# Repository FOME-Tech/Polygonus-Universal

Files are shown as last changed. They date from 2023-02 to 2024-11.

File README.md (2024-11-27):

# Polygonus-Universal

Basic pinout for the bosch 88 pin plug intended for universal use.  

## NOT COMPATIBLE WITH ANY PNP APPLICATION  

## NOTE - 88pin plug is now hard to source as it seems to be NLA from Aliexpress. 
Hardware tested ok on the first fabrication but is now obsolete due to connector sourcing issues. 
Board is provided as is for reference of if someone wants to fabricate and source their own connectors.

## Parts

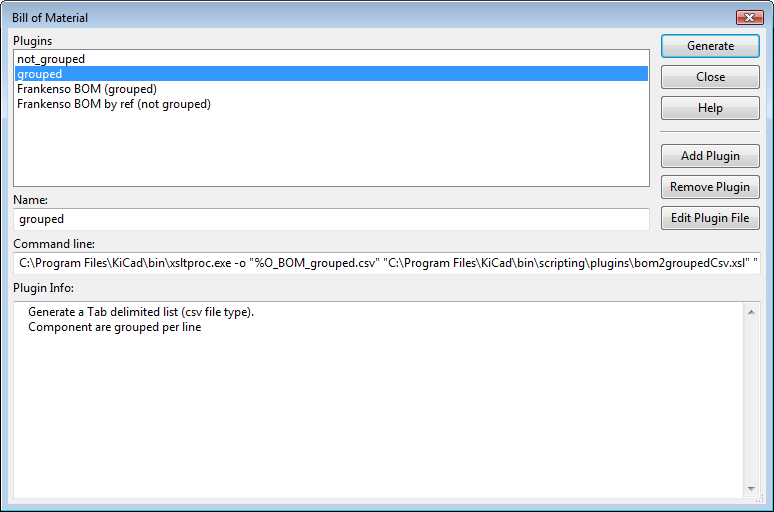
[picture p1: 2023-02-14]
kicad-libraries/BOM_related/Kicad_BOM_grouped.png

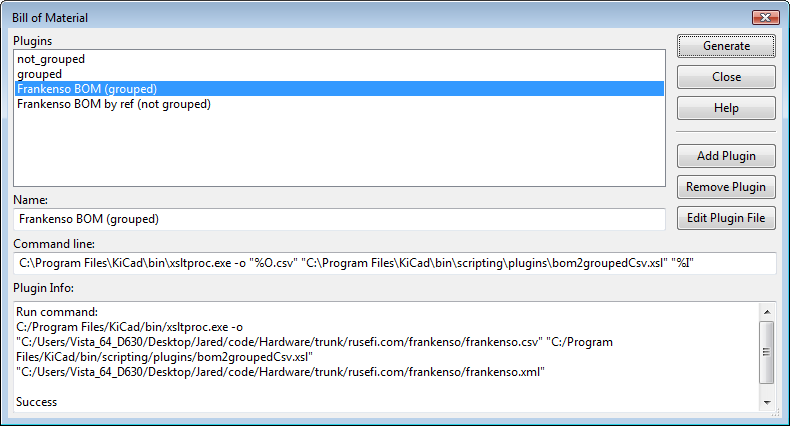
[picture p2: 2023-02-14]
kicad-libraries/BOM_related/Kicad_BOM_grouped_Frankenso.png

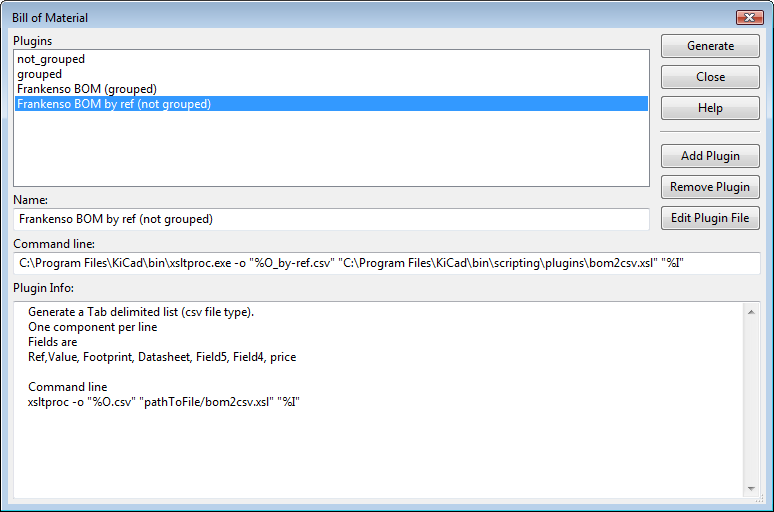
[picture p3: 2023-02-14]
kicad-libraries/BOM_related/Kicad_BOM_Not_grouped_Frankenso.png

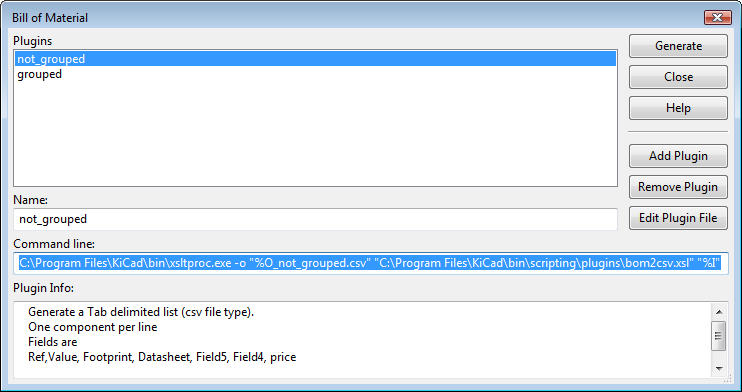
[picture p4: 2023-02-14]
kicad-libraries/BOM_related/Kicad_BOM_Not_grouped.png

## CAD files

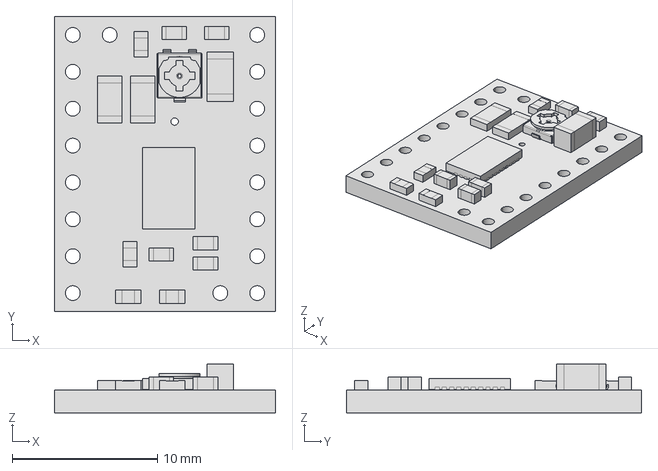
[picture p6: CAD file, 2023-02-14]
kicad-libraries/3d/Misc/drv8880-stepper-motor-driver-carrier.FCStd
15.2 x 20.3 x 3.37 mm

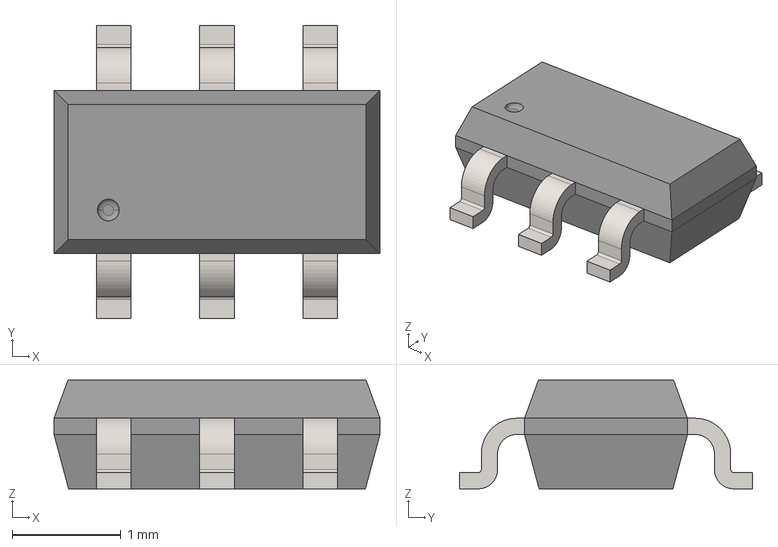
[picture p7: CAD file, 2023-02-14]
kicad-libraries/3d/TSOP-6.step
3.00 x 2.70 x 1.00 mm

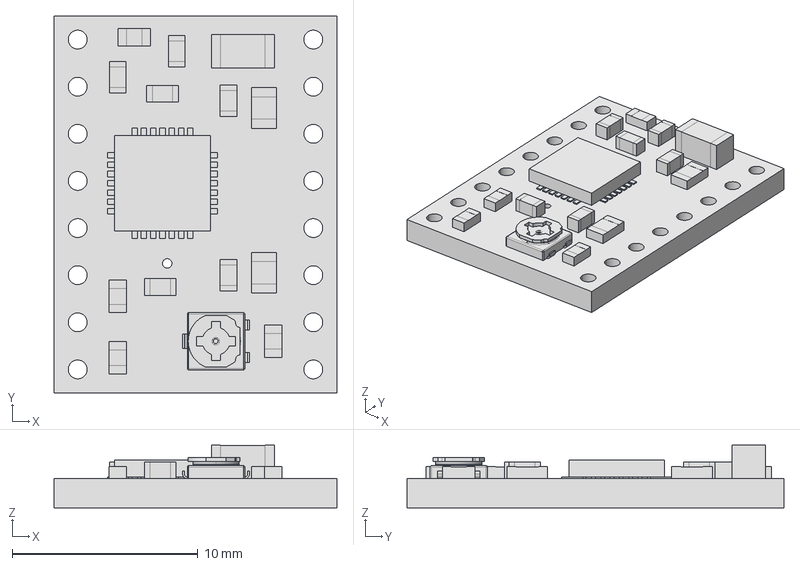
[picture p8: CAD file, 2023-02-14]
kicad-libraries/3d/Misc/a4988-stepper-motor-driver-carrier.FCStd
15.2 x 20.3 x 3.37 mm

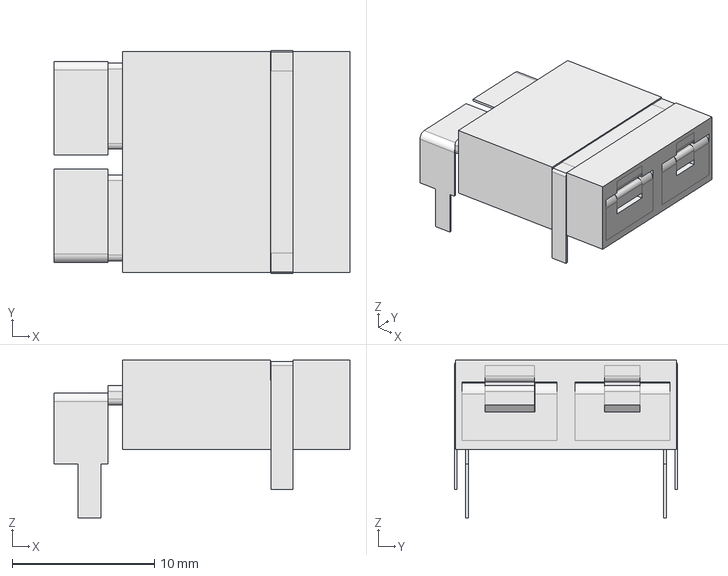
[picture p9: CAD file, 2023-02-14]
kicad-libraries/3d/TCPL_CONNECTOR_PCC-SMP.step
20.8 x 15.7 x 11.1 mm

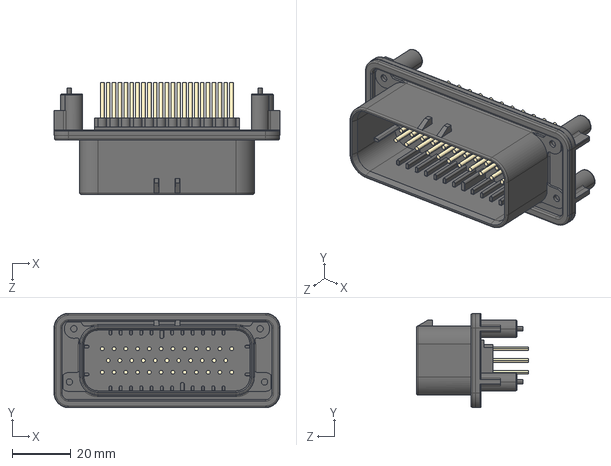
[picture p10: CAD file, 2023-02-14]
kicad-libraries/3d/c-1-776231-1-d-3d.STEP
76.9 x 32.1 x 38.0 mm

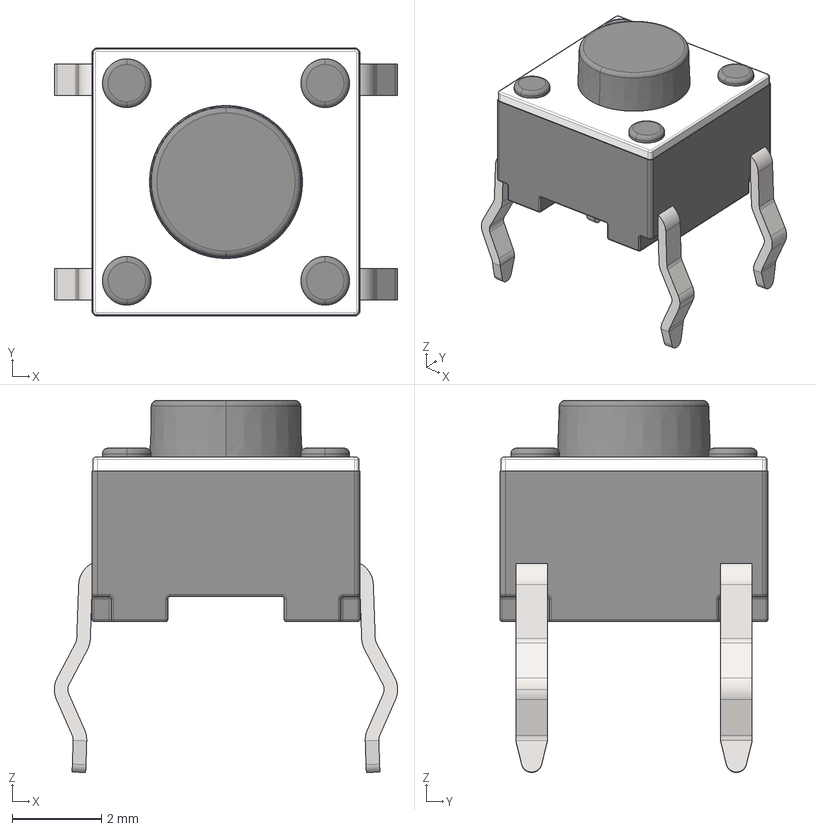
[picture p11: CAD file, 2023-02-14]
kicad-libraries/3d/tactileswitch-short.step
7.69 x 6.01 x 8.33 mm

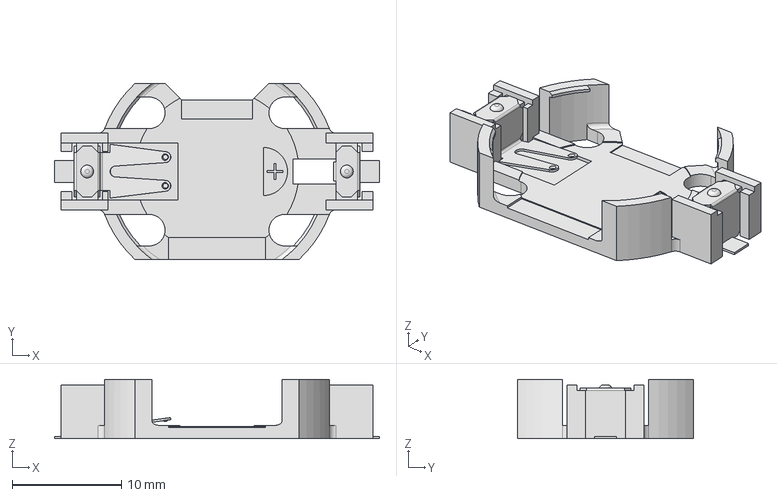
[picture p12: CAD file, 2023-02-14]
kicad-libraries/3d/BatHolder_SMTU2032.step
29.7 x 16.1 x 5.40 mm

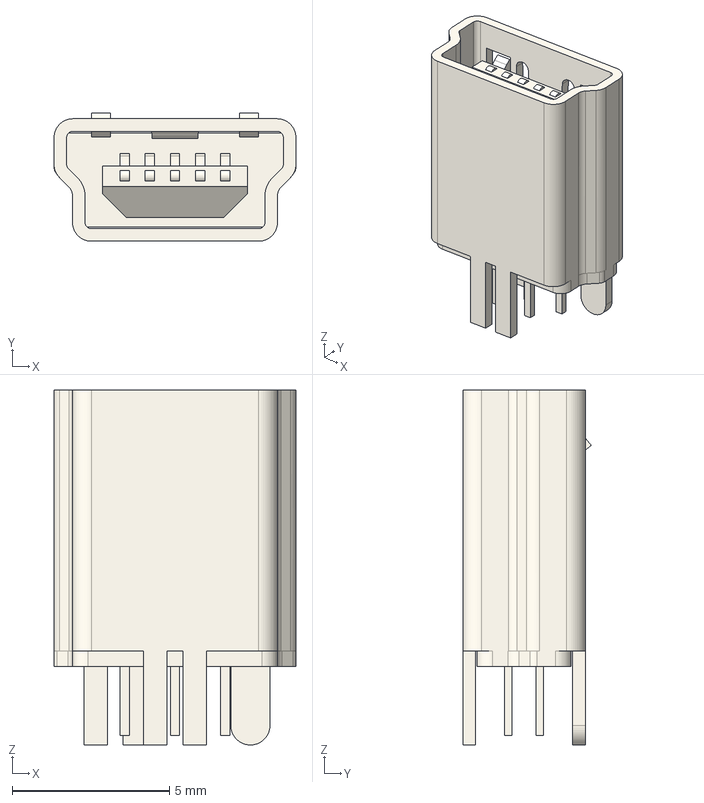
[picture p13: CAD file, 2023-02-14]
kicad-libraries/3d/USB_Vert_C-1734753-1.step
7.70 x 4.09 x 11.3 mm

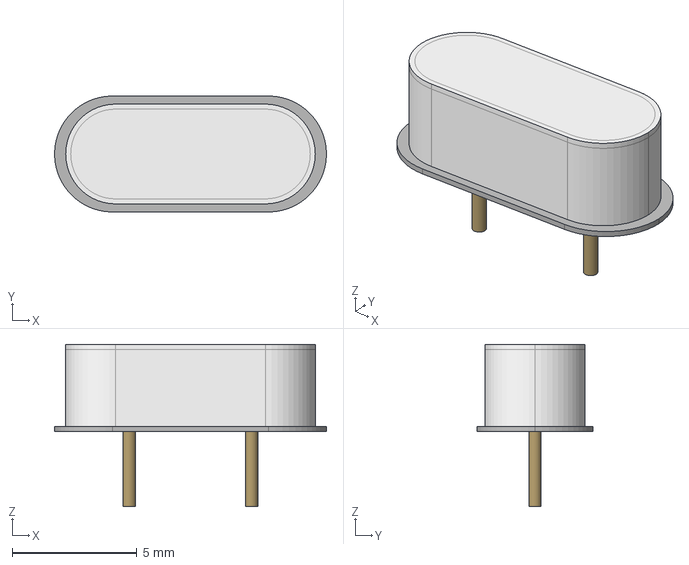
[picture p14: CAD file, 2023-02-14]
kicad-libraries/3d/HC18U.step
10.9 x 4.65 x 6.50 mm

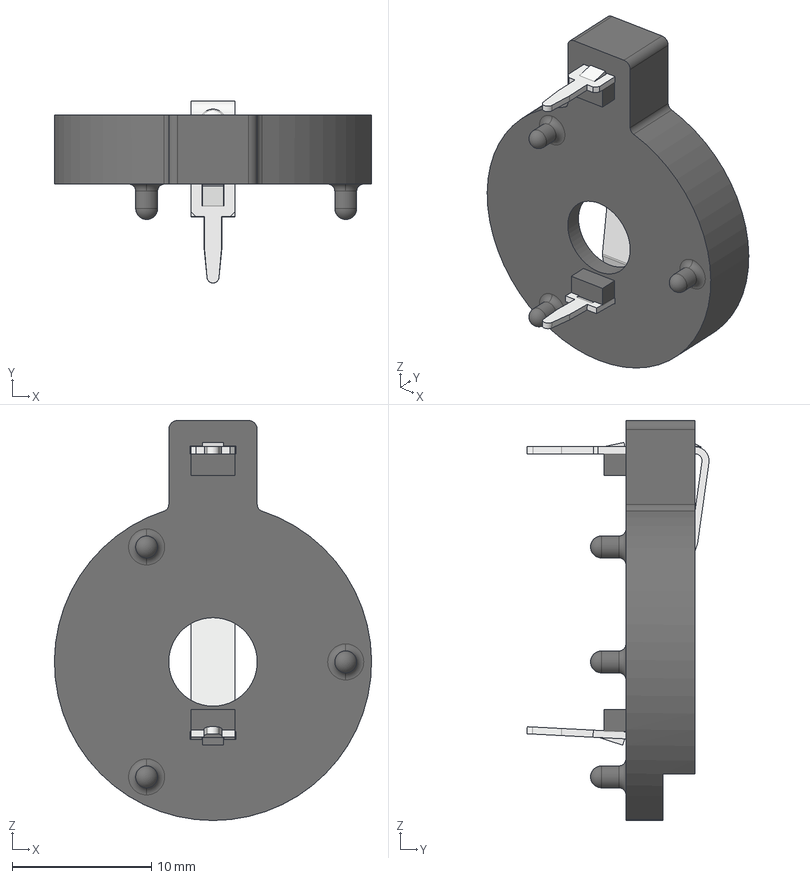
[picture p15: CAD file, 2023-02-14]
kicad-libraries/3d/MPD_CR2032.STEP
22.8 x 13.1 x 28.7 mm

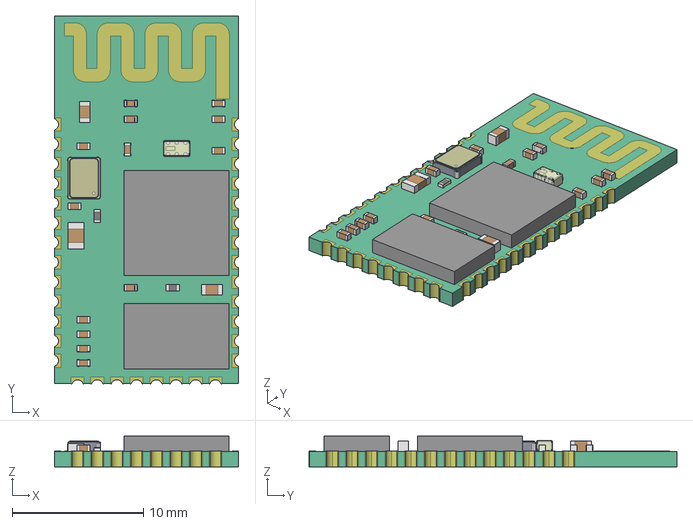
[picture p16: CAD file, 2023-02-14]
kicad-libraries/3d/itead_hc-05.step
14.0 x 28.0 x 2.35 mm

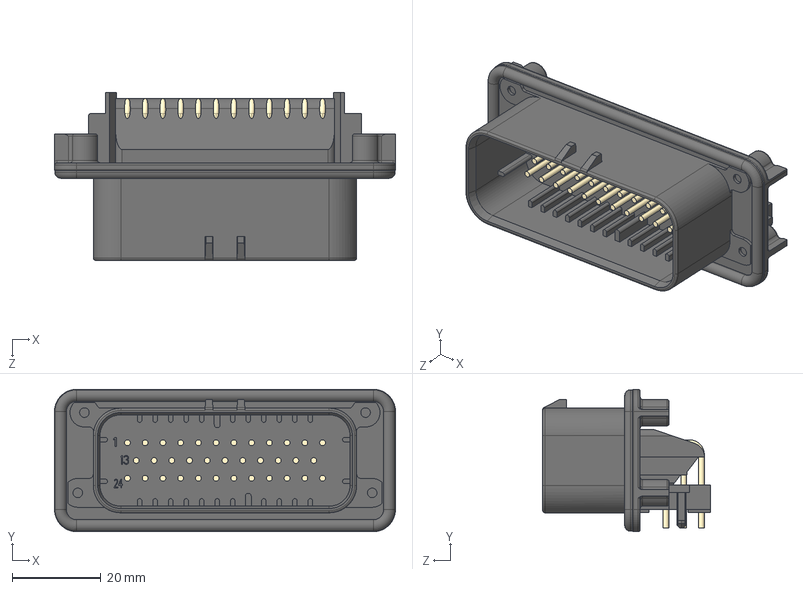
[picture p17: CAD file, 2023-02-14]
kicad-libraries/3d/AMPSEAL_35_RIGHT_ANGLE.STEP
76.9 x 32.1 x 37.8 mm

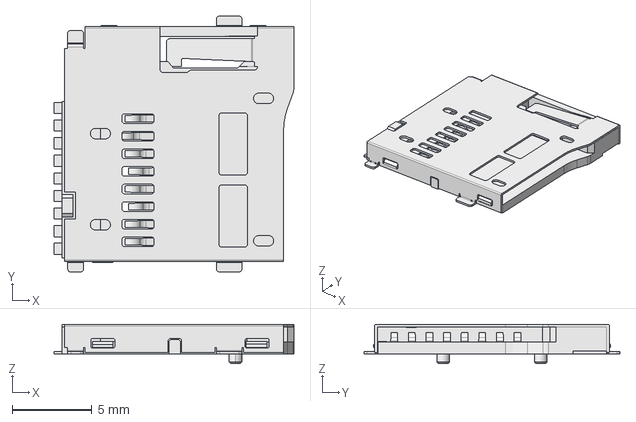
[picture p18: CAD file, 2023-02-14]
kicad-libraries/3d/micro_sd.step
15.0 x 16.0 x 2.44 mm

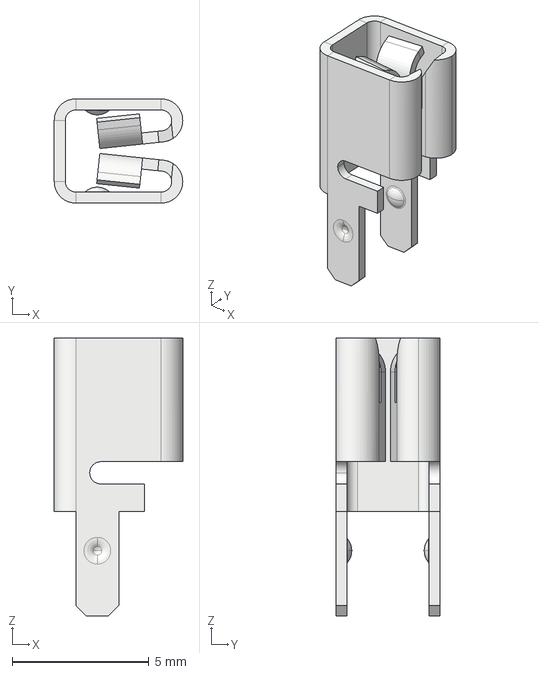
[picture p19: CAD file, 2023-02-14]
kicad-libraries/3d/keystone-3557.step
4.70 x 3.81 x 10.2 mm

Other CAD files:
kicad-libraries/3d/c-1-776231-2-d-3d.STEP
kicad-libraries/3d/AMPSEAL_35_STRAIGHT.STEP
kicad-libraries/3d/JoyStick_SKRHAA.step
kicad-libraries/3d/LCD_20x4.step
kicad-libraries/3d/AMPSEAL_23_STRAIGHT.stp
kicad-libraries/3d/LCD_20x4.FCStd
kicad-libraries/3d/LED_0805.step
kicad-libraries/3d/MPD_CR2032.FCStd
kicad-libraries/3d/Misc/a4988-stepper-motor-driver-carrier.stl
kicad-libraries/3d/Misc/drv8880-stepper-motor-driver-carrier.stl
kicad-libraries/3d/c-1-776228-1-e-3d.STEP

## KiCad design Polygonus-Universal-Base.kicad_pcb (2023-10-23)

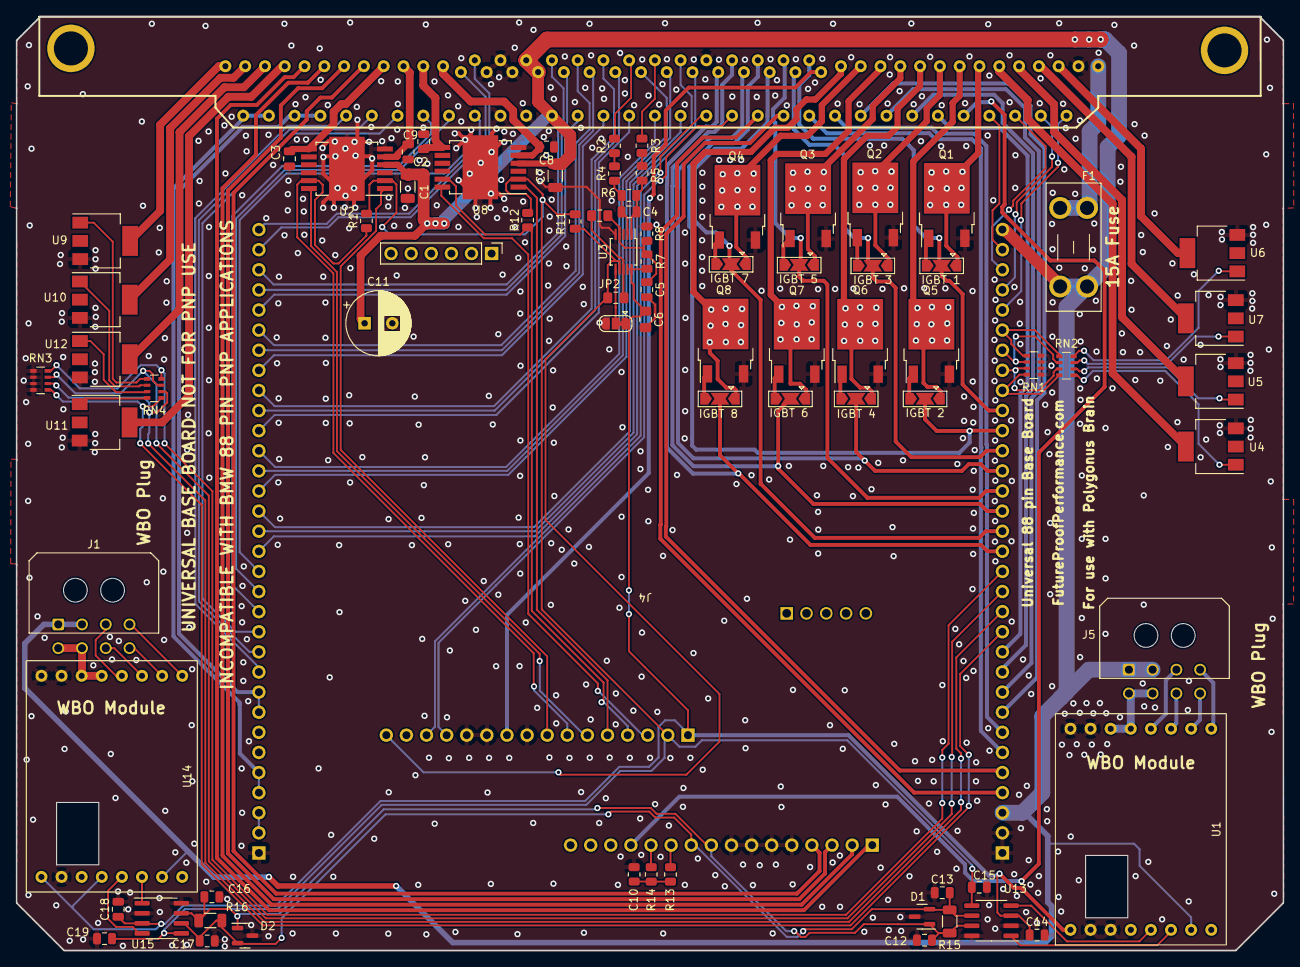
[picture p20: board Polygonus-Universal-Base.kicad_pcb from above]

Board: 2 copper layers, 160.0 x 118.0 mm, 78 parts (0 on the bottom side), 138 nets.

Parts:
C1, C7: 10u; C_1206_3216Metric
C2, C3, C8, C9: 10n; C_0805_2012Metric
C4: 1n; C_0805_2012Metric
C5: 1u; C_0805_2012Metric
C6: 100n; C_0805_2012Metric_Pad1.18x1.45mm_HandSolder
C10: 1u; R_0805_2012Metric
C11: 56u; CP_Radial_D8.0mm_P3.50mm
C12, C13, C16, C17: 47p; C_0805_2012Metric
C14, C15, C18, C19: 100n; C_0805_2012Metric
D1, D2: NUP2105L; SOT-23
F1: Fuse; Fuseholder_Blade_Mini_Keystone_3568
J1, J5: Conn_02x04_Top_Bottom; Molex_Micro-Fit_3.0_43045-0800_2x04_P3.00mm_Horizontal
J4: Polygonus_Plugs; Polygonus-With-USB-SWD
JP1, JP3, JP4, JP5, JP6, JP7, JP8, JP9: Jumper_3_Open; SolderJumper-3_P2.0mm_Open_TrianglePad1.0x1.5mm
JP2: Jumper_3_Bridged12; SolderJumper-3_P1.3mm_Bridged12_RoundedPad1.0x1.5mm
Motronic_88pin1: Motronic_88pin; 88Pin Motronic BMW
Q1, Q2, Q3, Q4, Q5, Q6, Q7, Q8: NGD8201AN; TO-252-2
R1, R12: 10k; R_0805_2012Metric
R2, R3, R4, R5, R11: 4.7k; R_0805_2012Metric
R6, R13, R14: DNP; R_0805_2012Metric
R7, R8: 1k; R_0805_2012Metric
R9, R10: DNP; R_0805_2012Metric_Pad1.15x1.40mm_HandSolder
R15, R16: 120; R_1206_3216Metric
RN1, RN2, RN3, RN4: 1k; R_Array_Convex_4x0603
U1, U14: f042_wideband_module
U2, U8: TLE9201SG; Infineon_PG-DSO-12-9
U3: MAX9924; MSOP-10_3x3mm_P0.5mm
U4, U5, U6, U7, U9, U10, U11, U12: VNL5090; SOT-223
U13, U15: TJA1051T-3; SOIC-8_3.9x4.9mm_P1.27mm

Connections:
+3.3V: C15.1, C19.1, J4.82, R1.2, R11.1, R12.2, U2.2 (VSO), U8.2 (VSO), U13.5 (VIO), U15.5 (VIO)
+5V: C6.1, C14.1, C18.1, J4.81, JP2.1 (A), R7.1, U1.1 (5V), U3.9 (INT_THRS), U3.10 (VCC), U13.3 (VCC), U14.1 (5V), U14.4 (SEL_2), U15.3 (VCC)
/5V_SENSOR_1: J4.40, J4.41, Motronic_88pin1.58, Motronic_88pin1.59
/5V_SENSOR_2: J4.36, J4.37, Motronic_88pin1.56, Motronic_88pin1.57
/12V_KEY: J4.90, Motronic_88pin1.21
/12V_MR: F1.1, Motronic_88pin1.28
/12V_MR_FUSE: C1.2, C7.2, C11.1, F1.2, J1.1, J1.2, J4.3, J4.32, J5.1, J5.2, Motronic_88pin1.10, Motronic_88pin1.37, Motronic_88pin1.68, U1.7 (VBatt_Sense), U2.4 (VS), U8.4 (VS), U14.7 (VBatt_Sense)
/12V_PROT: J4.34, J4.35
/AT1: J4.51, Motronic_88pin1.15
/AT2: J4.50, Motronic_88pin1.73
/AT3: J4.49, Motronic_88pin1.43
/AT4: J4.48, Motronic_88pin1.16
/AV1: J4.62, Motronic_88pin1.38
/AV2: J4.61, Motronic_88pin1.11
/AV3: J4.60, Motronic_88pin1.69
/AV4: J4.59, Motronic_88pin1.39
/AV5: J4.58, Motronic_88pin1.12
/AV6: J4.57, Motronic_88pin1.70
/AV7: J4.56, Motronic_88pin1.40
/AV8: J4.55, Motronic_88pin1.13
/AV9: J4.54, Motronic_88pin1.71
/AV10: J4.53, Motronic_88pin1.72
/AV11: J4.52, Motronic_88pin1.14
/CAN2+: C12.2, C16.2, D1.1 (K), D2.1 (K), J4.73, R15.1, R16.1, U13.7 (CANH), U15.7 (CANH)
/CAN2-: C13.1, C17.1, D1.2 (K), D2.2 (K), J4.74, R15.2, R16.2, U13.6 (CANL), U15.6 (CANL)
/CAN+: J4.93, Motronic_88pin1.75
/CAN-: J4.94, Motronic_88pin1.74
/CAN_RX: U1.5 (CAN_RX), U13.4 (RXD)
/CAN_RX2: U14.5 (CAN_RX), U15.4 (RXD)
/CAN_TX: U1.6 (CAN_TX), U13.1 (TXD)
/CAN_TX2: U14.6 (CAN_TX), U15.1 (TXD)
/CRANK +: Motronic_88pin1.41, R2.2
/CRANK -: Motronic_88pin1.42, R3.2
/DIGITAL_1: J4.47, Motronic_88pin1.65
/DIGITAL_2: J4.46, Motronic_88pin1.64
/DIGITAL_3: J4.45, Motronic_88pin1.63
/DIGITAL_4: J4.44, Motronic_88pin1.62
/DIGITAL_5: J4.43, Motronic_88pin1.61
/DIGITAL_6: J4.42, Motronic_88pin1.60
/ETB1_+: C8.2, Motronic_88pin1.34, U8.5 (OUT1)
/ETB1_-: C9.1, Motronic_88pin1.6, U8.7 (OUT2)
/ETB1_DIR: J4.85, U8.1 (DIR)
/ETB1_DIS: J4.84, R12.1, U8.11 (DIS)
/ETB1_PWM: J4.83, U8.12 (PWM)
/ETB2_+: C2.2, Motronic_88pin1.33, U2.5 (OUT1)
/ETB2_-: C3.1, Motronic_88pin1.5, U2.7 (OUT2)
/ETB2_DIR: J4.88, U2.1 (DIR)
/ETB2_DIS: J4.87, R1.1, U2.11 (DIS)
/ETB2_PWM: J4.86, U2.12 (PWM)
/ExtraLSA: Motronic_88pin1.1, U9.4 (Drain)
/ExtraLSB: Motronic_88pin1.29, U10.4 (Drain)
/ExtraLSC: Motronic_88pin1.2, U12.4 (Drain)
/ExtraLSD: Motronic_88pin1.30, U11.4 (Drain)
/HS1: J4.68, Motronic_88pin1.32
/HS2: J4.67, Motronic_88pin1.4
/HS3: J4.66, Motronic_88pin1.31
/HS4: J4.65, Motronic_88pin1.3
/HeaterNeg: J5.5, J5.6, U1.11 (HEATER-), U1.12 (HEATER-)
/HeaterNeg2: J1.5, J1.6, U14.11 (HEATER-), U14.12 (HEATER-)
/IGBT1: JP1.1 (A), Motronic_88pin1.25, Q1.2 (C)
/IGBT2: JP6.1 (A), Motronic_88pin1.52, Q5.2 (C)
/IGBT3: JP3.1 (A), Motronic_88pin1.24, Q2.2 (C)
/IGBT4: JP7.1 (A), Motronic_88pin1.51, Q6.2 (C)
/IGBT5: JP4.1 (A), Motronic_88pin1.23, Q3.2 (C)
/IGBT6: JP8.1 (A), Motronic_88pin1.50, Q7.2 (C)
/IGBT7: JP5.1 (A), Motronic_88pin1.22, Q4.2 (C)
/IGBT8: JP9.1 (A), Motronic_88pin1.49, Q8.2 (C)
/IGN1: J4.23, JP1.2 (C), Motronic_88pin1.48
/IGN2: J4.22, JP6.2 (C), Motronic_88pin1.46
/IGN3: J4.21, JP3.2 (C), Motronic_88pin1.20
/IGN4: J4.20, JP7.2 (C), Motronic_88pin1.18
/IGN5: J4.19, JP4.2 (C), Motronic_88pin1.47
/IGN6: J4.18, JP8.2 (C), Motronic_88pin1.45
/IGN7: J4.17, JP5.2 (C), Motronic_88pin1.19
/IGN8: J4.16, JP9.2 (C), Motronic_88pin1.17
/IGN9: J4.15, RN3.8 (R1.2), RN4.4 (R4.1)
/IGN10: J4.14, RN3.7 (R2.2), RN4.3 (R3.1)
/IGN11: J4.13, RN3.6 (R3.2), RN4.2 (R2.1)
/IGN12: J4.12, RN3.5 (R4.2), RN4.1 (R1.1)
/KNOCK_1: J4.63, Motronic_88pin1.35
/KNOCK_2: J4.64, Motronic_88pin1.7
/LS1: J4.4, Motronic_88pin1.76
/LS2: J4.5, Motronic_88pin1.77
/LS3: J4.6, Motronic_88pin1.78
/LS4: J4.7, Motronic_88pin1.79
/LS5: J4.8, Motronic_88pin1.80
/LS6: J4.9, Motronic_88pin1.81
/LS7: J4.10, Motronic_88pin1.82
/LS8: J4.11, Motronic_88pin1.83
/LS9: J4.24, RN1.8 (R1.2), RN2.4 (R4.1)
/LS9ADD: Motronic_88pin1.53, U4.4 (Drain)
/LS10: J4.25, RN1.7 (R2.2), RN2.3 (R3.1)
/LS10ADD: Motronic_88pin1.26, U5.4 (Drain)
/LS11: J4.26, RN1.6 (R3.2), RN2.2 (R2.1)
/LS11ADD: Motronic_88pin1.54, U7.4 (Drain)
/LS12: J4.27, RN1.5 (R4.2), RN2.1 (R1.1)
/LS12ADD: Motronic_88pin1.27, U6.4 (Drain)
/LS13: J4.28, Motronic_88pin1.88
/LS14: J4.29, Motronic_88pin1.87
/LS15: J4.30, Motronic_88pin1.86
/LS16: J4.31, Motronic_88pin1.85
/LSU_Ip: J5.3, U1.13 (LSU_ip)
/LSU_Ip2: J1.3, U14.13 (LSU_ip)
/LSU_Rtrim: J5.8, U1.15 (LSU_rtrim)
/LSU_Rtrim2: J1.8, U14.15 (LSU_rtrim)
/LSU_Un: J5.4, U1.16 (LSU_un)
/LSU_Un2: J1.4, U14.16 (LSU_un)
/LSU_Vm: J5.7, U1.14 (LSU_vm)
/LSU_Vm2: J1.7, U14.14 (LSU_vm)
/Perm_Live: J4.77, Motronic_88pin1.84
/RC1: J4.75, R13.2
/RC2: J4.76, R14.2
/VR1+: J4.96, R10.1, R11.2, U3.7 (COUT)
GND: C1.1, C2.1, C3.2, C5.2, C6.2, C7.1, C8.1, C9.2, C10.2, C11.2, C12.1, C13.2, C14.2, C15.2, C16.1, C17.2, C18.2, C19.2, D1.3 (A), D2.3 (A), J4.1, J4.2, J4.33, J4.69, J4.70, J4.71, J4.72, J4.89, J4.91, J4.92, JP2.3 (B), Motronic_88pin1.8, Motronic_88pin1.9, Motronic_88pin1.36, Motronic_88pin1.44, Motronic_88pin1.55, Motronic_88pin1.66, Motronic_88pin1.67, Q1.3 (E), Q2.3 (E), Q3.3 (E), Q4.3 (E), Q5.3 (E), Q6.3 (E), Q7.3 (E), Q8.3 (E), R8.1, RN1.1 (R1.1), RN1.2 (R2.1), RN1.3 (R3.1), RN1.4 (R4.1), RN3.1 (R1.1), RN3.2 (R2.1), RN3.3 (R3.1), RN3.4 (R4.1), U1.2 (GND), U1.3 (SEL_1), U1.9 (HEAT_GND), U1.10 (HEAT_GND2), U2.6 (GND), U2.13 (GND), U3.5 (GND), U4.3 (Source), U5.3 (Source), U6.3 (Source), U7.3 (Source), U8.6 (GND), U8.13 (GND), U9.3 (Source), U10.3 (Source), U11.3 (Source), U12.3 (Source), U13.2 (GND), U13.8 (S), U14.2 (GND), U14.9 (HEAT_GND), U14.10 (HEAT_GND2), U15.2 (GND), U15.8 (S)
unnamed: C10.1, R13.1, R14.1
unnamed: JP1.3 (B), Q1.1 (G)
unnamed: JP2.2 (C), U3.6 (ZERO_EN)
unnamed: JP3.3 (B), Q2.1 (G)
unnamed: JP4.3 (B), Q3.1 (G)
unnamed: JP5.3 (B), Q4.1 (G)
unnamed: JP6.3 (B), Q5.1 (G)
unnamed: JP7.3 (B), Q6.1 (G)
unnamed: JP8.3 (B), Q7.1 (G)
unnamed: JP9.3 (B), Q8.1 (G)
unnamed: R2.1, R4.2
unnamed: R3.1, R5.2
unnamed: RN2.8 (R1.2), U6.1 (Input)
unnamed: RN2.7 (R2.2), U7.1 (Input)
unnamed: RN2.6 (R3.2), U5.1 (Input)
unnamed: RN2.5 (R4.2), U4.1 (Input)
unnamed: RN4.8 (R1.2), U11.1 (Input)
unnamed: RN4.7 (R2.2), U12.1 (Input)
unnamed: RN4.6 (R3.2), U10.1 (Input)
unnamed: RN4.5 (R4.2), U9.1 (Input)
unnamed: C5.1, R7.2, R8.2, R9.2, U3.4 (BIAS)
unnamed: R9.1, R10.2, U3.8 (EXT)
unnamed: C4.2, R5.1, R6.1, U3.1 (IN+)
unnamed: C4.1, R4.1, R6.2, U3.2 (IN-)

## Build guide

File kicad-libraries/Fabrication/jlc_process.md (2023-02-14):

See https://github.com/rusefi/hw_modular/tree/master/lowside/gerbers for an example of how things are set.

jlc_prepare-*.bat scripts use grep, gawk & sed so Cygwin is required.

# Bill Of Materials

1) See ../BOM_related file for KiCad to produce XXX.csv KiCad BOM.

1) Use prepare_fabricate.bat to invoke jlc_prepare_bom.bat produce XXX-bom.csv final JLC BOM file.

# Placement

1) Use KiCad to produce XXX-top-pos.csv file

1) Use prepare_fabricate.bat to invoke jlc_prepare_position.bat to produce XXX-cpl.csv final JLC placement file.

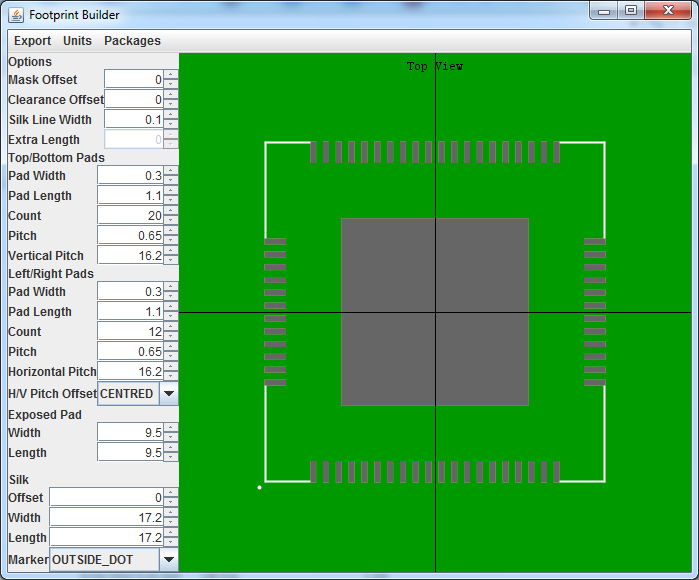
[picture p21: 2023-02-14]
kicad-libraries/HiQUAD64_footprint_builder.png

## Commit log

2023-02-14 Stripped board in prep for layout
    [AMPSEAL_23_STRAIGHT.stp, AMPSEAL_35_RIGHT_ANGLE.STEP, AMPSEAL_35_STRAIGHT.STEP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]
2023-02-14 Made the board
    [Lowside Adder.kicad_sch, Polygonus-Universal-Base.kicad_pcb, Polygonus-Universal-Base.kicad_sch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]
2023-02-14 Competed board
    [Lowside Adder.kicad_sch, Polygonus-Universal-Base.kicad_pcb, Polygonus-Universal-Base.kicad_sch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]
2023-10-05 Modified IGBTs and routed smart coils
    [Lowside Adder.kicad_sch, Polygonus-Universal-Base.kicad_pcb, Polygonus-Universal-Base.kicad_sch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]
2023-10-20 updated and fixed, check JLC exports
    [Polygonus-Universal-Base-CuBottom.gbr, Polygonus-Universal-Base-CuTop.gbr, Polygonus-Universal-Base-EdgeCuts.gbr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]
2023-10-22 All fixed up for JLC
    [IGBT outputs.kicad_sch, Lowside Adder.kicad_sch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]
2023-10-22 Moved folders and added schematics or die
    [Polygonus-Universal-Base-CuBottom.gbr, Polygonus-Universal-Base-CuTop.gbr, Polygonus-Universal-Base-EdgeCuts.gbr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]
2023-10-23 Fixed 12V_RAW and added grounds for sensors
    [Lowside Adder.kicad_sch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]
2023-10-23 convert to kicad7, add jumpers for direct drive igbt output
    [IGBT outputs.kicad_sch, Lowside Adder.kicad_sch, Polygonus-Universal-Base.kicad_pcb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]
2023-10-23 tweak silk
    [Polygonus-Universal-Base.kicad_pcb]
2023-10-23 silkscreen/erc tweaks
    [Polygonus-Universal-Base.kicad_pcb]
2023-10-23 fix labels in schematic
    [IGBT outputs.kicad_sch, Polygonus-Universal-Base.kicad_sch]
2023-10-23 wideband symbol/footprint
2023-10-23 fix wideband library, ERC, DRC
    [Lowside Adder.kicad_sch, Polygonus-Universal-Base.kicad_pcb, Polygonus-Universal-Base.kicad_sch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]
2023-10-23 4-layer-ify the board, do some rerouting for 4 layer goodness
2023-10-24 Add freewheel diodes, power pins explanation comment
    [Lowside Adder.kicad_sch, Polygonus-Universal-Base.kicad_sch, VR conditioner.kicad_sch]
2023-10-24 silkscreen cleanup
2023-10-24 route widebands to main connector
    [Polygonus-Universal-Base.kicad_sch]
2023-10-24 adjust silkscreen label for igbts
2023-10-31 Real minor tidy up around 12v/lowsides
2023-11-01 Fixed WBO pin allocation
    [Polygonus-Universal-Base.kicad_sch]
2023-11-01 Added DRV8825 footprint
    [Polygonus-Universal-Base.kicad_sch]
2023-11-02 adjusted a couple of parameters to suit JLC
2023-11-02 default set HS
    [Polygonus-Universal-Base.kicad_sch]
2023-11-02 stepper ls direct to logic pins
    [Polygonus-Universal-Base.kicad_sch]
2023-11-12 export cleanup
    [BOM-Polygonus-Universal-Base.csv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]
2023-11-12 production files v1.0
    [BOM-Polygonus-Universal-Base.csv, Polygonus-Universal-Base.kicad_sch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]
2023-11-12 schematic title blocks
    [IGBT outputs.kicad_sch, Lowside Adder.kicad_sch, Polygonus-Universal-Base.kicad_sch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]
2023-11-19 Revert "updates"
    This reverts commit 8b03831b9e3606a0c51971a3414fde57c991d853.
    [quicklib_TLE6244.csv, test-bom.csv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]
2023-11-22 Removed the alleged via and 2 redundant schematic tags
    [Polygonus-Universal-Base.kicad_sch]
2023-11-29 Fixed the vias and ran a quick DRC
    Only silk screen overlaps and complaints about the IGBT and stepper selection footprints remain, I don't think this is critical, just warnings.
2024-01-14 fixed stepper pullup and updated silkscreen
    [Polygonus-Universal-Base.kicad_sch]
2024-01-14 Generated V2.0 Gerbs for prototype order
    [BOM-Polygonus-Universal-Base.csv, Polygonus-Universal-Base.kicad_sch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]
2024-11-27 Removed fab files to prevent YOLO orders, added note to readme.
    [BOM-Polygonus-Universal-Base.csv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]
